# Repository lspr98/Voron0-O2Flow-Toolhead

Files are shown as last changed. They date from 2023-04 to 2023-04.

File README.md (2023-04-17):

# Voron0-O2Flow-Toolhead
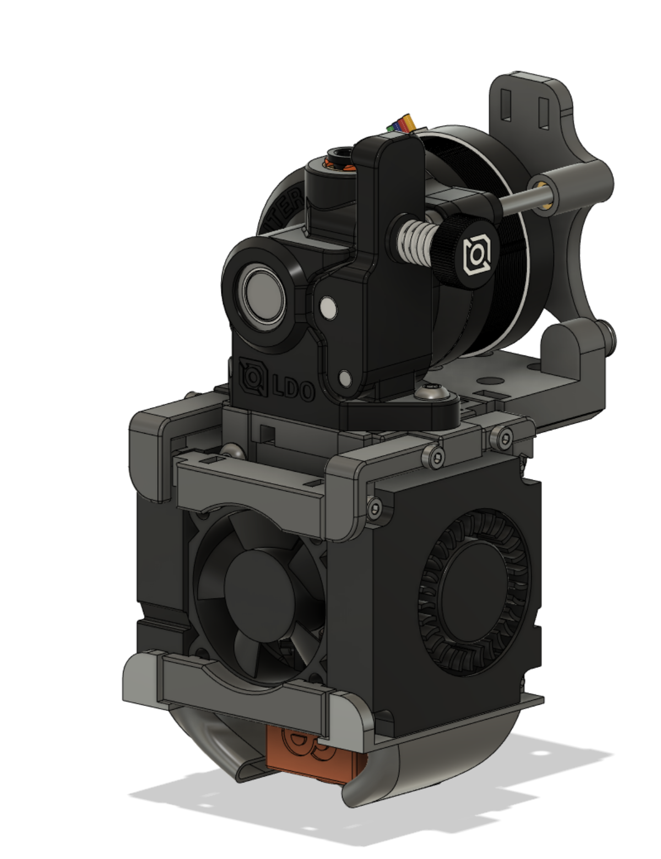
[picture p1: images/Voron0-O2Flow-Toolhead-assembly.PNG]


## Highlights
- 2x 4010 blower fans for increased part cooling performance
- compatible with original Voron 0.2 hotend mounts
- easy maintenance due to screw-together-design

## Important notes
Due to the larger fans, you lose roughly 10mm of buildarea in Y direction, resulting in (XYZ) 120mm x 110mm x 120mm

# Instructions

## Printing
Use the default Voron 0.2 printing settings.
|Settings|Value|
|---|---|
|Wall count|4|
|Top/Bottom Layers|5|
|Layer Height|0.2mm|
|Material|ABS/ASA|
|Infill|40%|

Parts starting with **V0_S_** need support for printing.
You need to print one piece of every part.

## Assembly
Please refer to the .STEP assembly.

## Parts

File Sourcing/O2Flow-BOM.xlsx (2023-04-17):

Category | Description | Quantity | Notes | Location/Function
Fasteners | M2 Nut | 12 | Note: when buying cheap M2 screws/nuts, be sure to order some extra as they often arrive with faulty threads | slotted into the fan brackets and the extruder mount
 | M3 Nut | 4 |  | slotted into the extruder mount and the Xcarriage
 | M2x6 SHCS | 8 | includes the 4 screws required for mounting the x carriage | four fix the Xcarriage to the rail, four fix the blower fans at the side facing the X-rail
 | M2x12 SHCS | 8 | longer ones may also work, check assembly for clearance | four fix the upper fan mounts to the extruder mount, four fix the front fan mounts
 | M3x30 SHCS | 2 | make sure it is fully threaded! | connect the orbiter to the backplate upper brass inserts
 | M3x35 BHCS | 2 |  | connect the hotend mount and extruder mount to the Xcarriage
 | M3x6 FHCS | 2 |  | connect the blackplate to the Xcarriage brass inserts
 | M3x10 BHCS | 2 |  | connect the orbiter to the extruder mount
 | M2.5x8 SHCS | 4 | Hotend mounting screws for Dragon HF (those usually come with the hotend) | connect hotend to hotend mount
 | M3 Brass inserts - short M3x5x4 (same as V0.2 build) | 4 | those are the same as specified in the V0.2 BOM. You may reuse leftovers | two go into the back of the Xcarriage and two go into the backplate
Elecronics | 3010 axial fan | 1 |  | front, hotend cooling fan
 | 4010 blower fan | 2 |  | left and right, part cooling fans
Misc | Zipties | 2 | for cable management on toolhead side. Buying spare ones is a good idea | organize and fix wires to the upper backplate
 | PTFE-Tube ID=2mm, OD=4mm, length=24mm | 1 | length may vary if you are using a hotend other than the dragon HF | creates filament path between orbiter and hotend
 | Orbiter 2.0 | 1 | rotate the stepper motor by 180° before assembly (wires facing upwards)
Printed | V0_O2Flow-Backplate | 1
 | V0_O2Flow-ExtruderMount | 1
 | V0_O2Flow-LowerFrontFanBracket | 1
 | V0_O2Flow-UpperFrontFanBracket | 1
 | V0_S_O2Flow-FanDuct | 1 | print with support (everywhere)
 | V0_S_O2Flow-FanDuctMirror | 1 | print with support (everywhere)
 | V0_S_O2Flow-UpperBackSideFanBracket | 1 | print with support (touching buildplate)
 | V0_S_O2Flow-UpperBackSideFanBracketMirror | 1 | print with support (touching buildplate)
 | V0_S_O2Flow-UpperFrontSideFanBracket | 1 | print with support (touching buildplate)
 | V0_S_O2Flow-UpperFrontSideFanBracketMirror | 1 | print with support (touching buildplate)
 | V0_S_O2Flow-XCarriage | 1 | print with support (touching buildplate)
External printed | Hotend Mount | 1 | Mounts can be found in the original Voron 0.2 repository or on printables/thingiverse

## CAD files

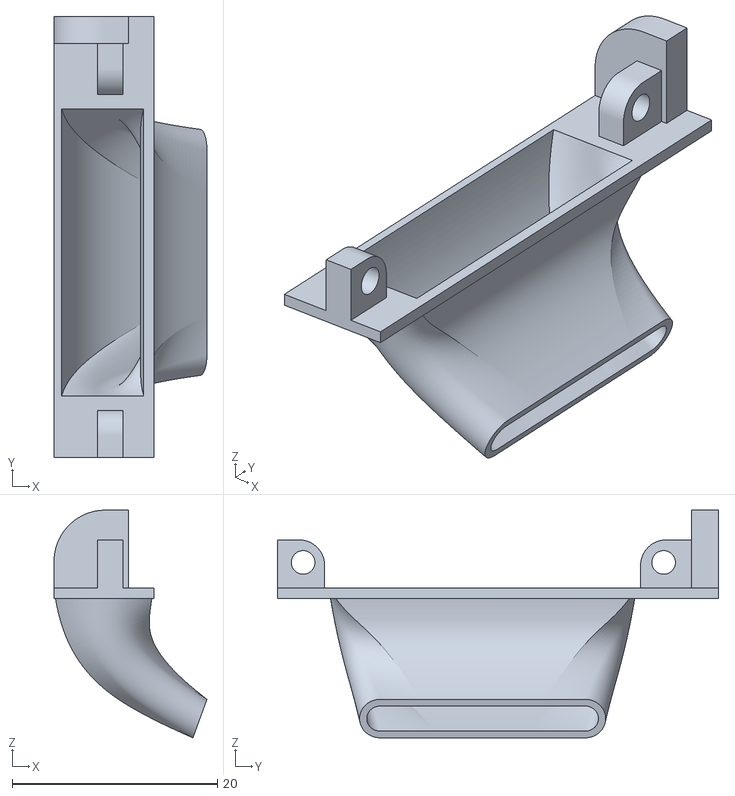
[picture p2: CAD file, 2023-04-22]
STL/V0_S_O2Flow-FanDuctMirror.stl
14.9 x 43.0 x 22.2

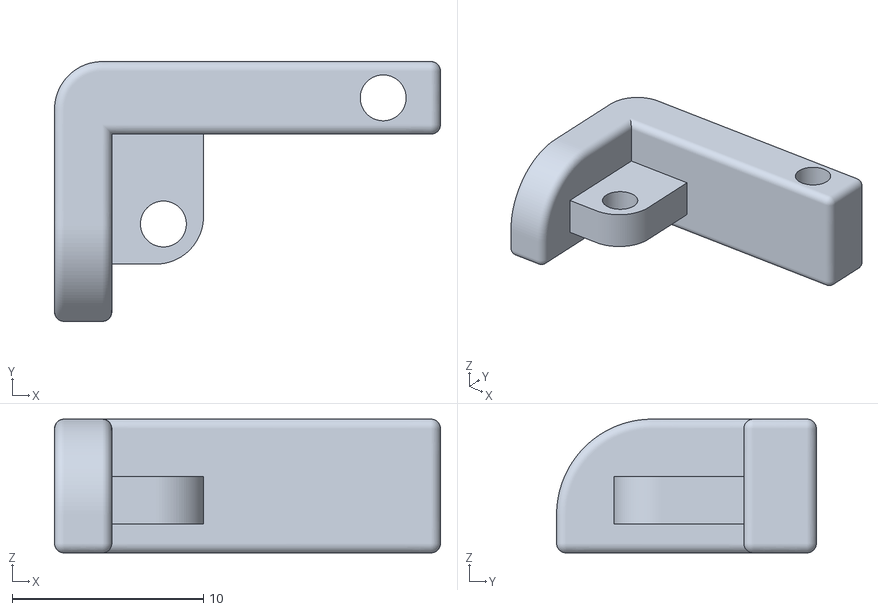
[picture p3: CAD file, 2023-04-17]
STL/V0_S_O2Flow-UpperFrontSideFanBracketMirror.stl
20.2 x 13.6 x 7.00

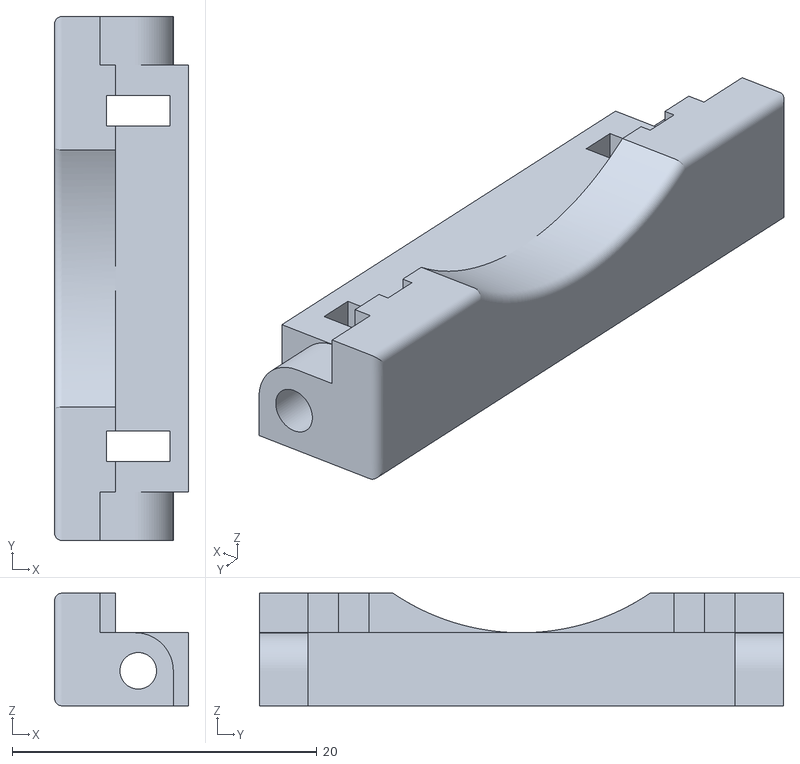
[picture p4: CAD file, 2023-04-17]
STL/V0_O2Flow-LowerFrontFanBracket.stl
8.80 x 34.4 x 7.40

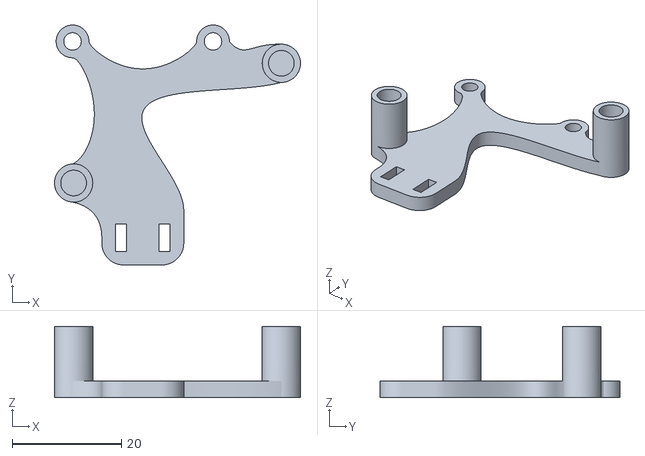
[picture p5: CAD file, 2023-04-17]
STL/V0_O2Flow-Backplate.stl
45.0 x 43.9 x 13.0

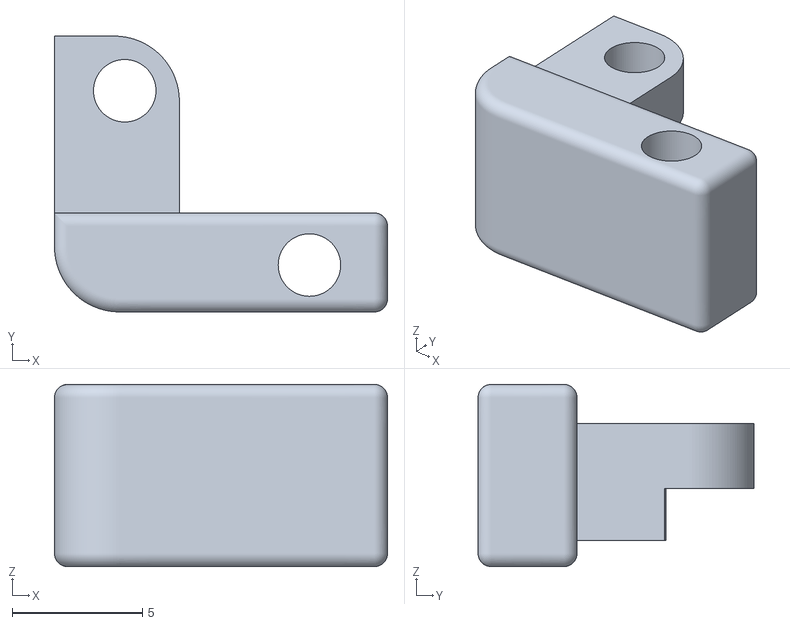
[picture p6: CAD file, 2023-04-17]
STL/V0_S_O2Flow-UpperBackSideFanBracket.stl
12.8 x 10.6 x 7.00

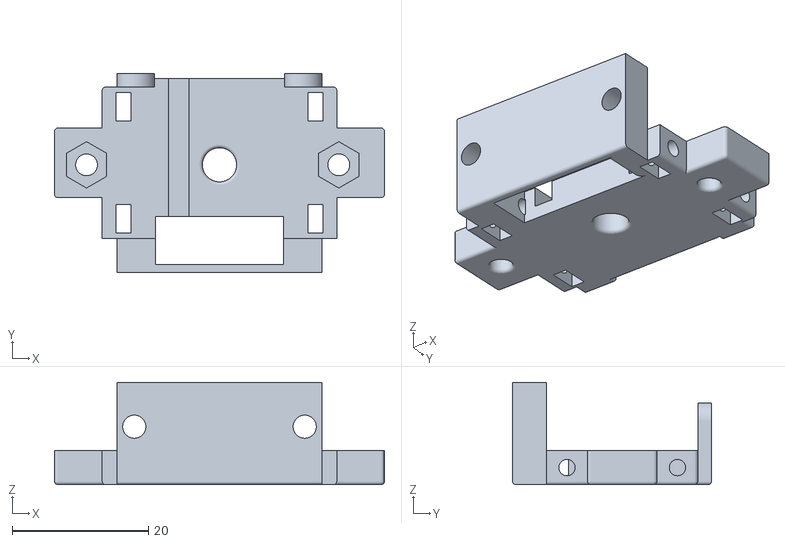
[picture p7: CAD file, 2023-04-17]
STL/V0_O2Flow-ExtruderMount.stl
48.4 x 29.2 x 15.0

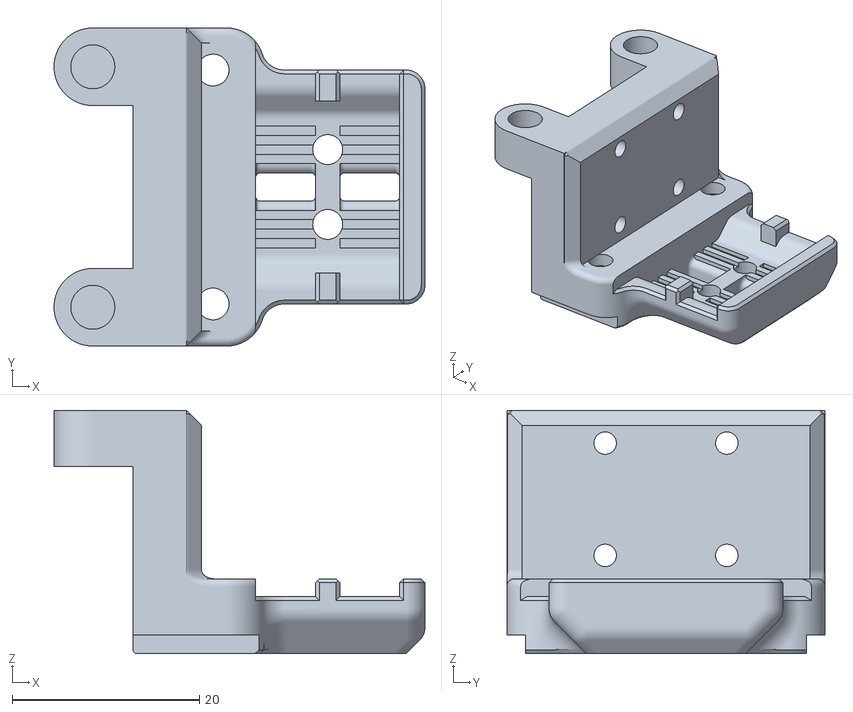
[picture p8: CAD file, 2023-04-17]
STL/V0_S_O2Flow-XCarriage.stl
39.7 x 34.0 x 26.0

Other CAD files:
STL/V0_S_O2Flow-FanDuct.stl
STL/V0_S_O2Flow-UpperFrontSideFanBracket.stl
STL/V0_O2Flow-UpperFrontFanBracket.stl
STL/V0_S_O2Flow-UpperBackSideFanBracketMirror.stl

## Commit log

2023-04-17 current version
    [O2Flow-BOM.xlsx, V0_O2Flow-Backplate.stl, V0_O2Flow-ExtruderMount.stl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]
2023-04-22 improved fan duct design
    [V0_S_O2Flow-FanDuct.stl, V0_S_O2Flow-FanDuctMirror.stl]
